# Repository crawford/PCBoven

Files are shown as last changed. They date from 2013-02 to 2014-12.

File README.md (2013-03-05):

PCBoven
=======

Reflow your toast.

'''Note''': Use this design at your own risk. I am not responsible for damaged
hardware or scorched appartments.

This is a USB host controlled DIY reflow oven. The aim of the project is to take
a cheap toaster oven and turn it into a temperature controlled reflow oven. The
oven itself is retrofitted with a custom control circuit which communicates over
USB with a host. The onboard oven controller is relatively simple, taking simple
commands (e.g. set target temperature) and reporting its state periodically. The
host application is the component that actually interpolates the reflow profile
and intructs the oven to hit target temperatures at certain times.

This implementation is broken into three components: firmware, device driver,
and control application, detailed below.

#Firmware#
The oven is controlled via the ATmega32u4 (in my case, the Adafruit ATmega32u4
breakout board), though another USB-enabled Atmel MCU could be specified in the
build process. The controller is designed to control two heating elements
independantly of one another in order to achieve a more even heating. Please,
refer to the [[schematic]] for details.

The firmware on the controller is communicates with the device driver using a
bulk endpoint (commands sent from the host to the device) and an interrupt
endpoint (periodic state (sent from the device to the host). Both endpoints
sent data using the same format (one for commands and one for state updates),
a packed structure of flags, for simplicity.

The firmware is responsible for properly controlling the temperature. The goal
is to quickly and accurately regulate the temperature with a fast response time
and low overshoot. Currently, there is no control algorithm and the performance
is less than ideal. Eventually, I'll implement a PD or PID controller (but no
autotuning (sorry T-Pain) so you'll have to provide your own values).

#Device Driver#
The device driver is written as a loadable kernel module for Linux (tested on
version 3.2 of the kernel). It registers itself as a miscellaneous device on
module load which creates the /dev/pcboven node (this node can only be used to
call ioctls). The driver also registers a USB device driver which gets loaded
when the oven controlled is connected to the host. The USB device driver
exposes a series of sysfs entries (e.g. probe temperature, fault flags, target
oven temperature) which can be used for debugging.

Control and monitoring of the oven is achieved through ioctl calls to the
/dev/pcboven node. This node is capable of sending SIGIO signals to the current
file owner. The signals are sent whenever a new state is received from the oven
or when the oven has been connected/disconnected. This mechanism is used
heavily by the control application and allows it to asynchronously monitor
connectivity and state.

#Control Application#
The control application is a relatively simple GUI front-end to this system.
It takes one command-line parameter, the path to the reflow profile. The profile
consists of a series of timestamps and temperatures which describe the intended
temperature/time curve (an example profile is included in the application
directory). The application interpolates the profile into a series of
temperature targets at one second intervals. This is what allows the oven to
smoothly follow the reflow curve.

The control application allows the user to monitor and control the reflow
sequence. At any point, the user can stop or start the sequence and view system
statistics. A temperature/time graph for both the target and actual oven
temperature is created in realtime. This allows the user to calibrate the oven
before use and to ensure that the sequence reached adequate temperatures during
use.

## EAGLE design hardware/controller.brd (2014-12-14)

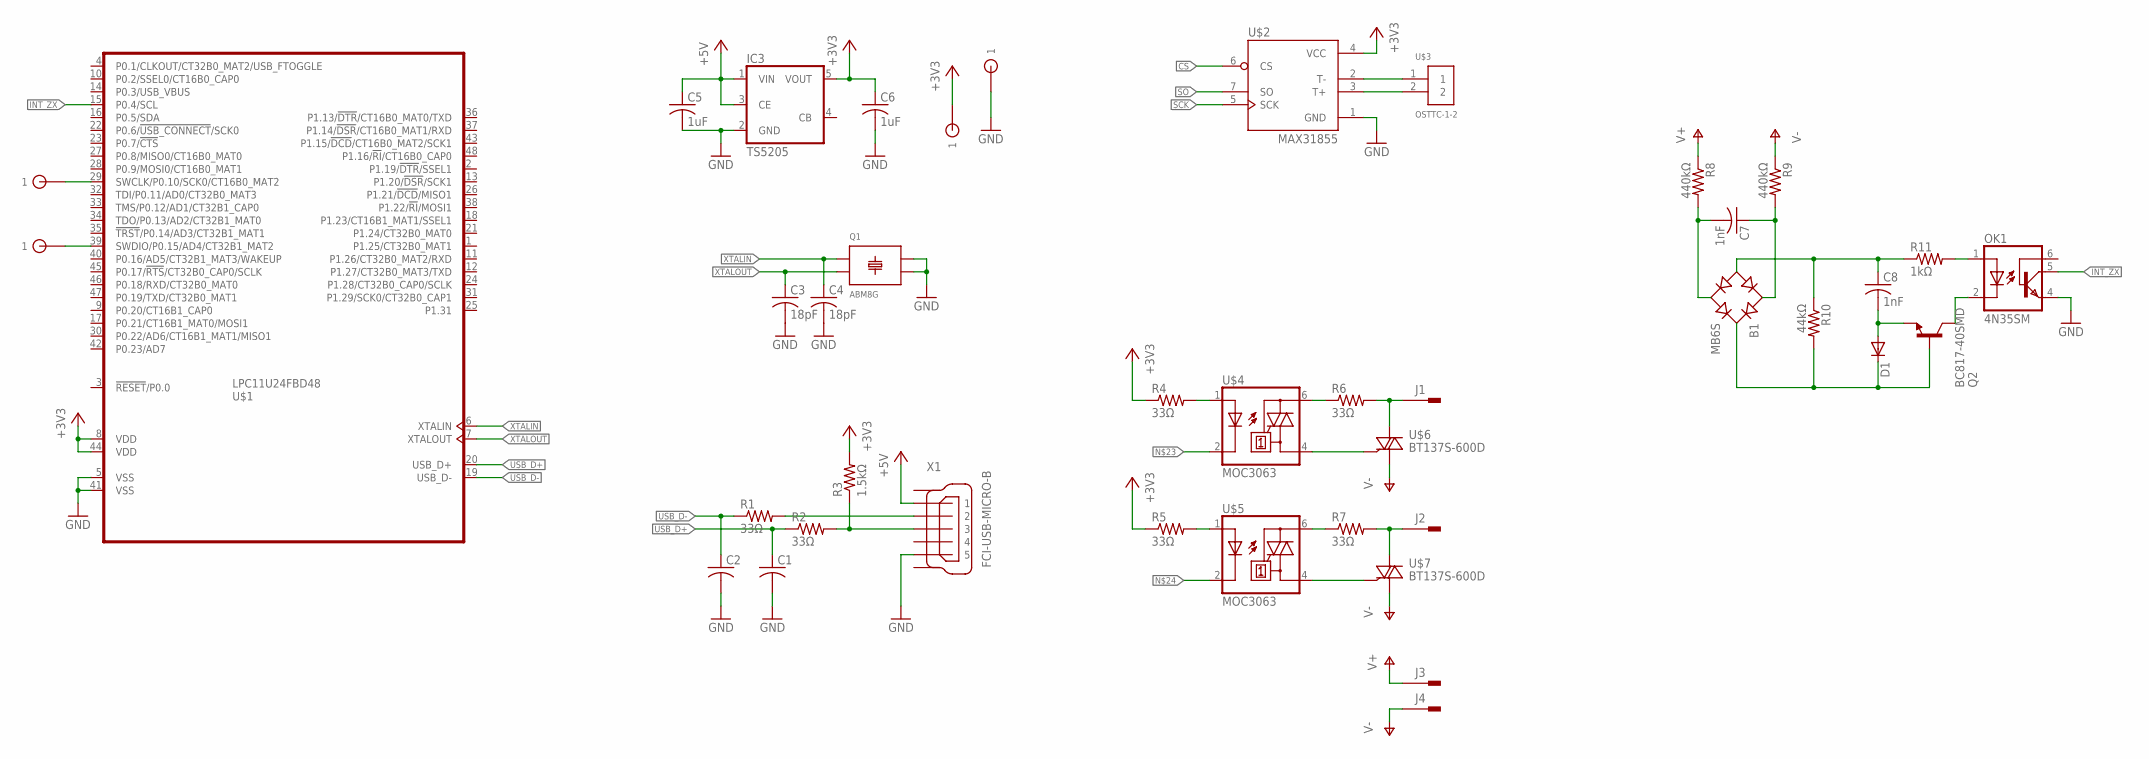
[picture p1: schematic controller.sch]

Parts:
B1: MB6S; SOIC-4
C1, C2: C-USC0402; C0402
C3, C4: 18pF; C0402K
C5, C6: 1uF; C0402K
C7, C8: 1nF; C0402K
D1: DIODE-SOD80C; SOD80C
IC3: TS5205; SOT25
J1, J2, J3, J4: PIN2F061.100; F061.100
OK1: 4N35SM; DIL6-SMD
Q1: ABM8G; SMD-4
Q2: BC817-40SMD; SOT23-BEC
R1, R2, R4, R5, R6, R7: 33Ω; R0402
R3: 1.5kΩ; R0402
R8, R9: 440kΩ; R0402
R10: 44kΩ; R0402
R11: 1kΩ; R0402
TP1, TP2, TP6, TP7: TESTPOINT; TESTPOINT-SMD
U$1: LPC11U24FBD48; LQFP48
U$2: MAX31855; SO08
U$3: OSTTC-1-2
U$4, U$5: MOC3063; SMD6
U$6, U$7: BT137S-600D; TO-252
X1: FCI-USB-MICRO-B; FCI-MICRO-USB-B

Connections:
+3V3: C6.1, IC3.5 (VOUT), R3.2, R4.1, R5.1, TP6.1, U$1.8 (VDD), U$1.44 (VDD), U$2.4 (VCC)
+5V: C5.1, IC3.1 (VIN), IC3.3 (CE), X1.1
CS: U$2.6 (CS)
G1: X1.M1 (G1)
G2: X1.M2 (G2)
GND: C1.2, C2.2, C3.2, C4.2, C5.2, C6.2, IC3.2 (GND), OK1.4 (EMI), Q1.2 (GND1), Q1.4 (GND2), TP7.1, U$1.5 (VSS), U$1.41 (VSS), U$2.1 (GND), X1.5
INT_ZX: OK1.5 (COL), U$1.15 (P0.4/SCL)
unnamed: R6.1, U$4.6 (A2)
unnamed: J2.A1, J2.A2, R7.2, U$7.1 (A2)
unnamed: R1.2, X1.2
unnamed: U$2.2 (T-), U$3.1
unnamed: U$2.3 (T+), U$3.2
unnamed: TP2.1, U$1.29 (SWCLK/P0.10/SCK0/CT16B0_MAT2)
unnamed: R2.2, R3.1, X1.3
unnamed: R7.1, U$5.6 (A2)
unnamed: TP1.1, U$1.39 (SWDIO/P0.15/AD4/CT32B1_MAT2)
unnamed: R4.2, U$4.1 (A)
unnamed: R5.2, U$5.1 (A)
unnamed: J1.A1, J1.A2, R6.2, U$6.1 (A2)
unnamed: U$4.4 (A1), U$6.2 (G)
unnamed: U$5.4 (A1), U$7.2 (G)
unnamed: B1.-, C8.1, R10.1, R11.1
unnamed: B1.+, D1.C, Q2.B, R10.2
unnamed: B1.~1 (AC1), C7.1, R9.2
unnamed: B1.~2 (AC2), C7.2, R8.2
unnamed: OK1.1 (A), R11.2
unnamed: OK1.2 (C), Q2.C
unnamed: C8.2, D1.A, Q2.E
SCK: U$2.5 (SCK)
SO: U$2.7 (SO)
USB_D+: C1.1, R2.1, U$1.20 (USB_D+)
USB_D-: C2.1, R1.1, U$1.19 (USB_D-)
V+: J3.A1, J3.A2, R8.1
V-: J4.A1, J4.A2, R9.1, U$6.3 (A1), U$7.3 (A1)
XTALIN: C4.1, Q1.1, U$1.6 (XTALIN)
XTALOUT: C3.1, Q1.3 (2), U$1.7 (XTALOUT)

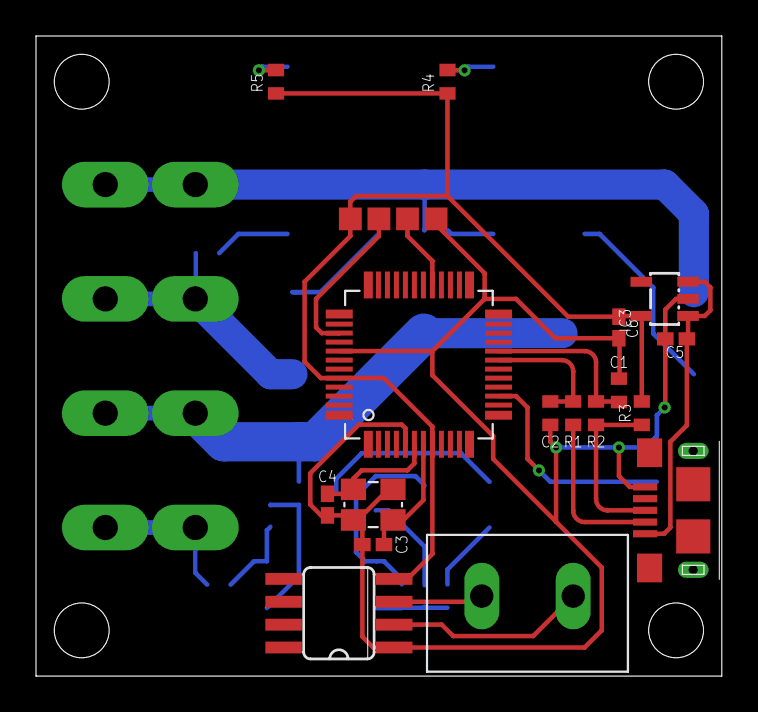
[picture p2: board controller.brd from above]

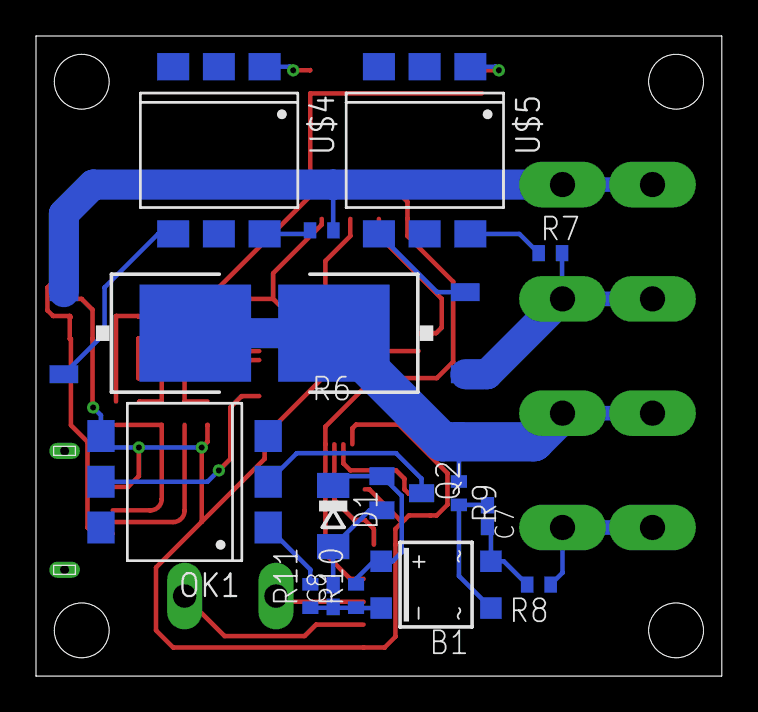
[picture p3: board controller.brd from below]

Board: 2 copper layers, 38.1 x 35.6 mm, 41 parts (16 on the bottom side), 31 nets.

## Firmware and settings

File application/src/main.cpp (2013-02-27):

#include <QApplication>
#include <iostream>
#include "controlpanel.h"

int main(int argc, char *argv[])
{
	QApplication a(argc, argv);

	if (qApp->arguments().count() != 2) {
		std::cerr << "Usage: "
		          << qApp->arguments().first().toUtf8().data()
		          << " reflow-profile"
		          << std::endl;
		return -1;
	}

	ControlPanel w;
	w.show();
	return a.exec();
}

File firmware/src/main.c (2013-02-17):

#include <avr/io.h>
#include <avr/power.h>
#include <avr/wdt.h>
#include <util/delay.h>
#include <stdbool.h>
#include <LUFA/Drivers/Board/LEDs.h>
#include "descriptors.h"
#include "max31855.h"
#include "filament.h"

#define TEMP_READ_RATE 1
#define FILAMENT_TOP_PORT    PORTF
#define FILAMENT_TOP_PIN     0
#define FILAMENT_BOTTOM_PORT PORTF
#define FILAMENT_BOTTOM_PIN  1

void platform_init();
int process_reading(struct max31855_result reading, int16_t target);

volatile bool g_take_readings;

int main()
{
	int16_t target_probe_temp = 0;
	bool filaments_enabled = false;
	struct max31855_result reading;
	struct filament top_filament =
	{
		.port = &FILAMENT_TOP_PORT,
		.pin  = FILAMENT_TOP_PIN,
		.on   = false
	};
	struct filament bottom_filament =
	{
		.port = &FILAMENT_BOTTOM_PORT,
		.pin  = FILAMENT_BOTTOM_PIN,
		.on   = false
	};
	int result;

	platform_init();
	max31855_init();
	USB_Init();
	LEDs_Init();

	g_take_readings = false;
	sei();

	while (true) {
		Endpoint_SelectEndpoint(OUT_EPNUM);
		if (Endpoint_IsOUTReceived()) {
			target_probe_temp = Endpoint_Read_16_LE();
			filaments_enabled = !!Endpoint_Read_8();

			if (!filaments_enabled) {
				filament_turn_off(&top_filament);
				filament_turn_off(&bottom_filament);
			}

			Endpoint_ClearOUT();
		}
		if (g_take_readings) {
			g_take_readings = false;

			Endpoint_SelectEndpoint(IN_EPNUM);

			if (max31855_read(&reading)) {
				LEDs_ToggleLEDs(LEDS_ALL_LEDS);
				filament_turn_off(&top_filament);
				filament_turn_off(&bottom_filament);
			} else {
				result = process_reading(reading, target_probe_temp);
				if (filaments_enabled) {
					if (result > 0)
						filament_turn_on(&top_filament);
					else
						filament_turn_off(&top_filament);

					if (result > 1)
						filament_turn_on(&bottom_filament);
					else
						filament_turn_off(&bottom_filament);
				}
			}

			Endpoint_Write_16_LE(reading.probe_temp);
			Endpoint_Write_16_LE(reading.internal_temp);
			Endpoint_Write_8(reading.short_vcc);
			Endpoint_Write_8(reading.short_gnd);
			Endpoint_Write_8(reading.open_circuit);
			Endpoint_Write_8(top_filament.on);
			Endpoint_Write_8(bottom_filament.on);

			Endpoint_ClearIN();
		}
		USB_USBTask();
	}

	__builtin_unreachable();
}

void platform_init()
{
	/* Disable watchdog if enabled by bootloader/fuses */
	MCUSR &= ~(1 << WDRF);
	wdt_disable();

	/* Disable clock division */
	clock_prescale_set(clock_div_1);

	/* Timer Initialization */
	OCR1A = F_CPU / 1024 / TEMP_READ_RATE;

	TCCR1A = 0;
	TCCR1B = (1 << WGM12 |   // CTC
	          1 << COM1A1 |  // Clear on compare match
	          0x05);         // Set the pre-scaler to 1024
	TIMSK1 = (1 << OCIE1A);  // Enable interrupt at set point
}

int process_reading(struct max31855_result reading, int16_t target)
{
	if (reading.probe_temp * 2 < target)
		return 2;

	if (reading.probe_temp < target)
		return 1;

	return 0;
}

ISR(TIMER1_COMPA_vect, ISR_BLOCK) {
	g_take_readings = true;
}

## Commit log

2013-02-07 Changing read rate to 1Hz
2013-02-07 Adding initial filament code -Added a braindead temperature control implementation
2013-02-09 Got USB comm working -Reverted LUFA back to a previous version (following up with Dean) -Set up poll timer
    [main.c]
2013-02-13 Finishing MAX31855 driver -Verified in the freezer and the oven
2013-02-14 Committing the USB driver
2013-02-14 Changing USB device product id
2013-02-15 Adding driver support for filaments -Fixed bug in filament code
    [main.c]
2013-02-15 Adding target temp to driver -Adding filament enable to firmware
2013-02-16 Changing pin definitions -Changed pins to the board pinout -Upped USB current to support two relays (200mA each)
2013-02-17 Finalizing prototype -Fixed sys entries -Fixed pinout -Fixed error handling
    [main.c, max31855.c]
2013-02-22 Adding ioctl support to application and driver
2013-02-23 Fixing driver -Transmit whenever temperature or filaments are changed
2013-02-27 Reflow sequence works properly now -Fixed temperatures
2013-03-01 Added dummy device
2013-03-01 Fixing probe/remove behavior for application
2014-12-13 hardware: initial attempt with relays
    [controller.brd, controller.sch]
2014-12-14 hardware: first attempt with triacs
    [controller.brd, controller.sch]
